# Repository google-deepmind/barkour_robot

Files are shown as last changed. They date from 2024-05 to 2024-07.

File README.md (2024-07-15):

# Barkour Robot

The Barkour Robots are a series of agile quadruped robots developed by Google
DeepMind to support various research projects.

This repository contains the design assets (CAD, PCBA designs, assembly
instructions...) and core software (firmware and low level code) of the Barkour
robots.

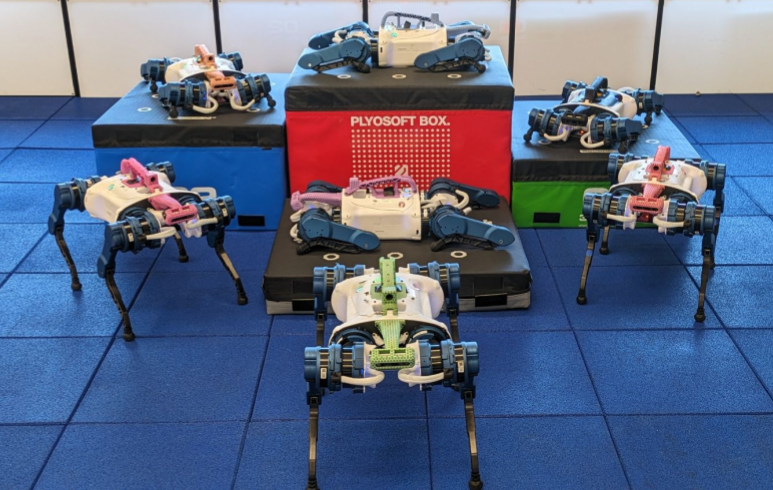
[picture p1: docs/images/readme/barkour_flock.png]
Barkour Robots Hanging Out


## Contents

Detailed documentation is available in the `docs/` folder:

*   [Robot getting started/basic usage guide](docs/getting_started.md)
*   Software:
    *   [Embedded software (firmware)](docs/firmware.md)
    *   [Configuring EtherCAT](docs/ethercat_config.md)
    *   [Motor control example](docs/motor_control.md)
*   Hardware:
    *   [Hardware overview and specs](docs/hardware_overview.md)
    *   [Electronics (PCBA) design files](hardware/electronics)
    *   [Range of motion](docs/barkour_rom.md)
    *   [Cable assembly drawings (WireViz)](hardware/cable_drawings)
*   Robot assembly guides:
    *   [Barkour robot assembly](docs/full_barkour_robot_assembly.md)
    *   [Actuator assembly and setup](docs/actuator_assembly_and_setup.md)
    *   [Hip cover assembly](docs/hipcover_assembly_instructions.md)
    *   [Leg linkage assembly](docs/leglinkage_assembly_instructions.md)
    *   [Wireless E-stop (STO) assembly](docs/wsto_assembly.md)
    *   [IMU configuration](docs/imu_config.md)
    *   [Actuated head assembly](docs/actuated_head_assembly.md)

Mechanical CAD files and simulation environments are available at the following
links:

*   [CAD model](https://gdm.onshape.com/documents/2587dbf423d784b45437b14a/v/b07bb08c3dc8b02bae21b866/e/bdcd5797385cee9e4f78dfef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)
*   Simulation:
    *   [MuJoCo model](https://github.com/google-deepmind/mujoco_menagerie/tree/main/google_barkour_vb)
    *   [MJX tutorial](https://github.com/google-deepmind/mujoco/blob/main/mjx/tutorial.ipynb)

### Mechanical design (CAD models)

We release 2 versions of the Barkour Robot. One version has a fixed head, the
other has an actuated head with a mouth (gripper). You can find the
[CAD models here](https://gdm.onshape.com/documents/2587dbf423d784b45437b14a/v/b07bb08c3dc8b02bae21b866/e/bdcd5797385cee9e4f78dfef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)
for both versions.

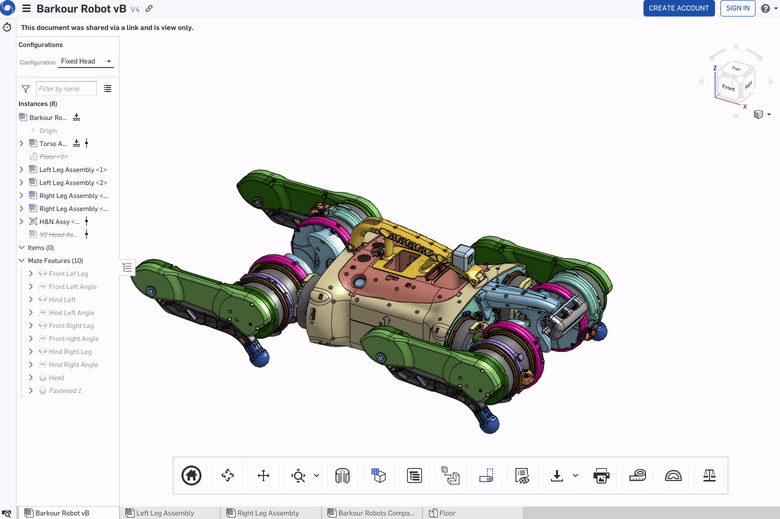
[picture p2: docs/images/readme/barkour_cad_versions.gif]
Barkour Robot CAD Model


### Hardware Usage

Please take a look at the [getting started guide](docs/getting_started.md).

### Simulation

The simulation models were previously released as part of the MuJoCo
[Menagerie](https://mujoco.readthedocs.io/en/stable/models.html). You can find
the MuJoCo model
[here](https://github.com/google-deepmind/mujoco_menagerie/tree/main/google_barkour_vb).

We support MJX for fast training on GPUs and TPUs. Please take a look at the
[MJX tutorial](https://github.com/google-deepmind/mujoco/blob/main/mjx/tutorial.ipynb)
to train a policy in minutes.

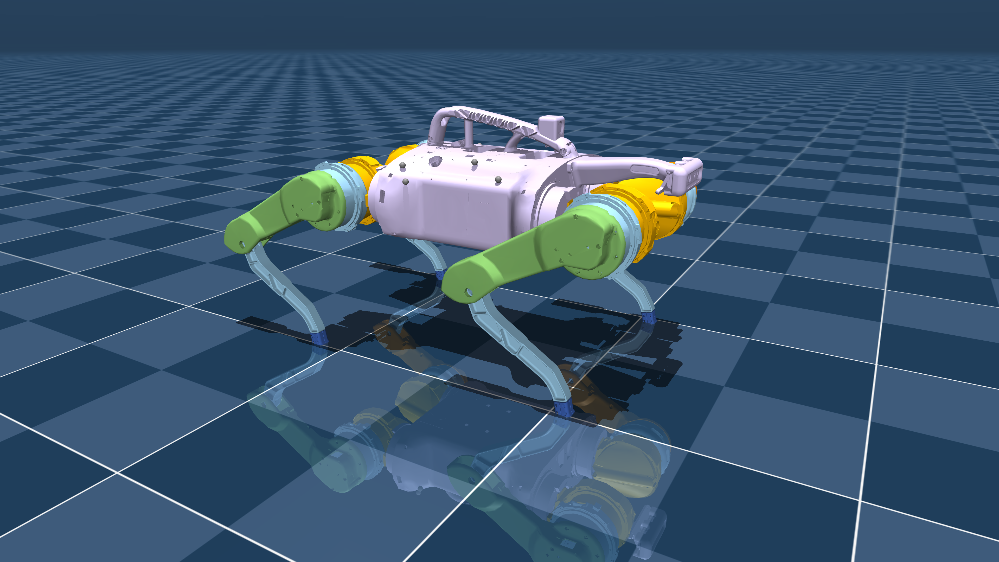
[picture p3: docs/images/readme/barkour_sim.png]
Barkour Robot Sim Model


### Electronics designs (PCBA)

We are including the schematics and PCB layout files for the custom electronics
on the Barkour robots. Take a look in the `hardware/electronics` folder.

You can find drawings of all custom cable assemblies in the
`hardware/cable_drawings` folder.

The Barkour robots use a custom motor driver that communicates with an on-board
computer over EtherCAT:

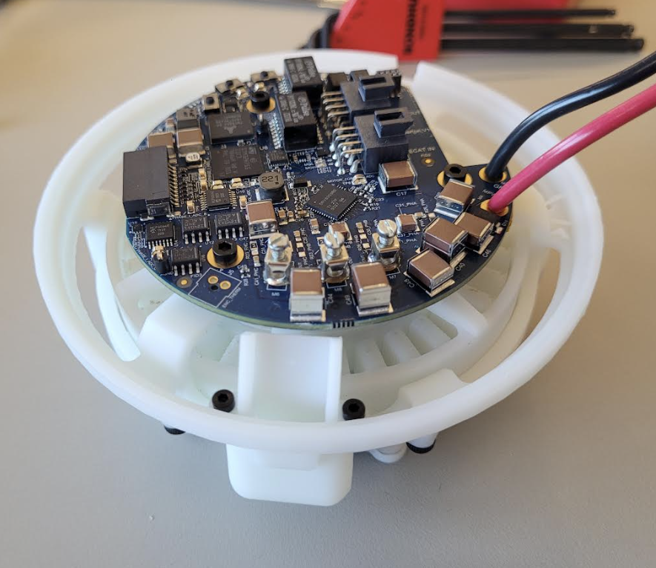
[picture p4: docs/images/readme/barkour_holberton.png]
Barkour Robot Motor Driver


### Assembly guides

We have a complete robot assembly guide to build robots from scratch. Take a
look at the following assembly guides:

-   [Barkour robot assembly](docs/full_barkour_robot_assembly.md)
-   [Actuator assembly and setup](docs/actuator_assembly_and_setup.md)
-   [Hip Cover Assembly instruction](docs/hipcover_assembly_instructions.md)
-   [Leg Linkage Assembly Instructions](docs/leglinkage_assembly_instructions.md)
-   [Wireless E-stop (STO) assembly](docs/wsto_assembly.md)

and here for the
[Bill of Materials (BOM)](hardware/barkour_robot_bill_of_materials.csv).

If you are curious about the actuated head, you can find the assembly
instructions [here](docs/actuated_head_assembly.md)

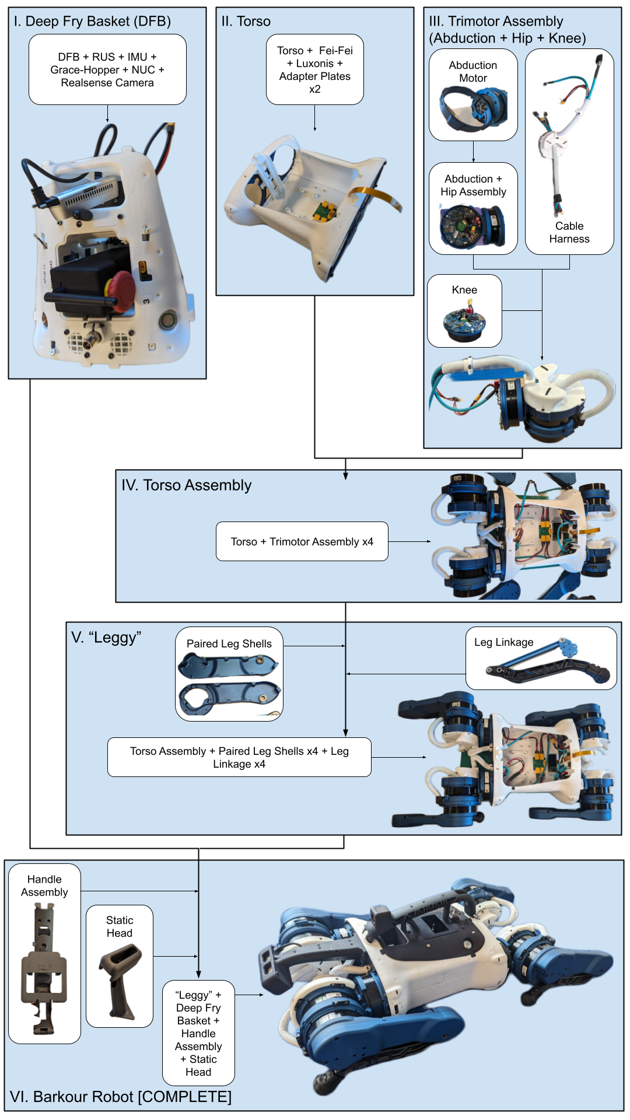
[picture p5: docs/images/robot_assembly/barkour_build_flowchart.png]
Barkour Robot Build Flowchart


### Embedded software and host side software

The Barkour motor drivers use custom firmware based on the
[Pigweed](https://pigweed.dev) open-source project. You can find the firmware in
the `actuator/firmware` folder and our firmware guide [here](docs/firmware.md).
We also provide [a hostside example](docs/motor_control.md) to control the
actuators via EtherCAT and a guide to
[configure EtherCAT](docs/ethercat_config.md).

## Hardware capabilities

The gifs below illustrate the hardware capabilities of the Barkour Robot
platform:

Two leg jump
Four leg jump
Dancing
Jump turn
Manipulating box lid
Pushing a cup of espresso
Push compensation
Tilt compensation
Picking up slippers
Closing dishwasher
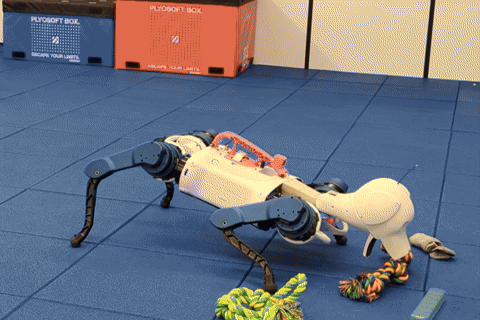
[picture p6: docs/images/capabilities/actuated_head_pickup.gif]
Picking up a toy

Picking up a pillbox
Picking up a shirt and dropping it off
Box climbing
Language to reward

## Older versions

This release contains the "vB" version of the Barkour Robot. As part of our
earlier work, we used an older version of the hardware, called "v0". You can
find the assets for the v0 version at the following links:

-   [CAD](https://gdm.onshape.com/documents/8bcc0544056aa5de830b6353/w/9f4df6916bccef9b9b882a52/e/9296b0bcf28e5f27569d4cdb),
-   [simplified CAD for URDF export](https://deepmind.onshape.com/documents/bd3aaf26c384d7d058cee090/w/9bd0468bf4dae717e9b02f17/e/6151d1e161dfa46066201d62),
-   [sim](https://github.com/google-deepmind/mujoco_menagerie/tree/main/google_barkour_v0),
-   [Barkour obstacle course sim](https://github.com/google-deepmind/mujoco_menagerie/tree/main/google_barkour_v0),
-   [Barkour course scoring script](https://github.com/google/brax/blob/main/brax/experimental/barkour/score_barkour.py).

## Citing this work

If you like this work or make use of our designs, please cite:

```latex
@article{caluwaerts2023barkour,
  title={Barkour: Benchmarking animal-level agility with quadruped robots},
  author={Caluwaerts, Ken and Iscen, Atil and Kew, J Chase and Yu, Wenhao and Zhang, Tingnan and Freeman, Daniel and Lee, Kuang-Huei and Lee, Lisa and Saliceti, Stefano and Zhuang, Vincent and others},
  journal={arXiv preprint arXiv:2305.14654},
  year={2023}
}
```

## License and disclaimer

Copyright 2024 DeepMind Technologies Limited

All software is licensed under the Apache License, Version 2.0 (Apache 2.0); you
may not use this file except in compliance with the Apache 2.0 license. You may
obtain a copy of the Apache 2.0 license at:
https://www.apache.org/licenses/LICENSE-2.0

All other materials are licensed under the Attribution-NonCommercial 4.0
International (CC BY-NC). You may obtain a copy of the CC BY-NC license at:
https://creativecommons.org/licenses/by-nc/4.0/legalcode

Unless required by applicable law or agreed to in writing, all software and
materials distributed here under the Apache 2.0 or CC BY-NC licenses are
distributed on an "AS IS" BASIS, WITHOUT WARRANTIES OR CONDITIONS OF ANY KIND,
either express or implied. See the licenses for the specific language governing
permissions and limitations under those licenses.

This is not an official Google product.

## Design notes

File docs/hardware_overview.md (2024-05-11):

# Hardware Overview

[TOC]

This page provides an overview of how the Barkour robots fit together.

## High-Level Hardware Specs

<table>
  <tr>
   <td>Weight
   </td>
   <td>≈ 14kg
   </td>
  </tr>
  <tr>
   <td>Onboard computer
   </td>
   <td>NUC11TNBv7
   </td>
  </tr>
  <tr>
   <td>Joint torque (nominal/peak)
   </td>
   <td>9Nm, ≥ 18Nm
   </td>
  </tr>
  <tr>
   <td>Joint velocity (peak)
   </td>
   <td>≥ 25rad/s
   </td>
  </tr>
  <tr>
   <td>Motor/battery voltage
   </td>
   <td>30-60V
   </td>
  </tr>
  <tr>
   <td>Sensor/compute voltage
   </td>
   <td>24V (max 200W, about 100W available)
   </td>
  </tr>
  <tr>
   <td>Bus
   </td>
   <td>EtherCAT (typically 1kHz bus cycle)
   </td>
  </tr>
  <tr>
   <td>Camera sensors
   </td>
   <td>RealSense d435i and Luxonis board with OAK-FFC camera module
   </td>
  </tr>
  <tr>
   <td>IMU
   </td>
   <td>1x 3DMCV7-AHRS (torso) + 12x LSM9DS1/LSM6DSO (motor drivers)
   </td>
  </tr>
  <tr>
   <td>Connectivity
   </td>
   <td>2x USB-C (Thunderbolt/USB4), 2.5Gb/s Ethernet (M12 connector), WiFi 6, Bluetooth 5.1, TP-Link UE306 Gigabit Ethernet Network Adapter (USB-to-RJ45) for EtherCAT.  <br/>
See NUC specs for additional connectivity available inside the torso.
   </td>
  </tr>
  <tr>
   <td>Motor
   </td>
   <td>T-motor AK80-9
   </td>
  </tr>
  <tr>
   <td>Wireless STO (E-stop) range
   </td>
   <td>≥ 50m
   </td>
  </tr>
</table>

Looking for the joint ranges or coordinate frame definitions? See
[Motion Conventions and Range of Motion](barkour_rom.md).

## System Diagram

The system diagram below shows the connectivity between the various parts of the
robot, mainly from an electrical point of view. It's a good place to start if
you want to understand how the robot works.

Archived version of system diagram

### NUC Port Allocation

Port allocation and cable selection should be kept consistent for all Barkour
robots.

Archived version of NUC port allocation diagram

### Torso Design Concept

The 3D printed torso consists of two main components: the torso (shell) itself
and the electronics basket.

## Motors

We are using a slightly modified version of the
[T-Motor AK80-9](https://store.tmotor.com/goods.php?id=982). Our variant has an
embedded thermistor and beefed up fasteners to prevent screws from coming loose.

We are not using the T-motor provided motor driver, but rather pair the motor
with the Gebru and Cortes boards (driver) and the Ada board (encoder), or the
Holberton board (driver + encoder).

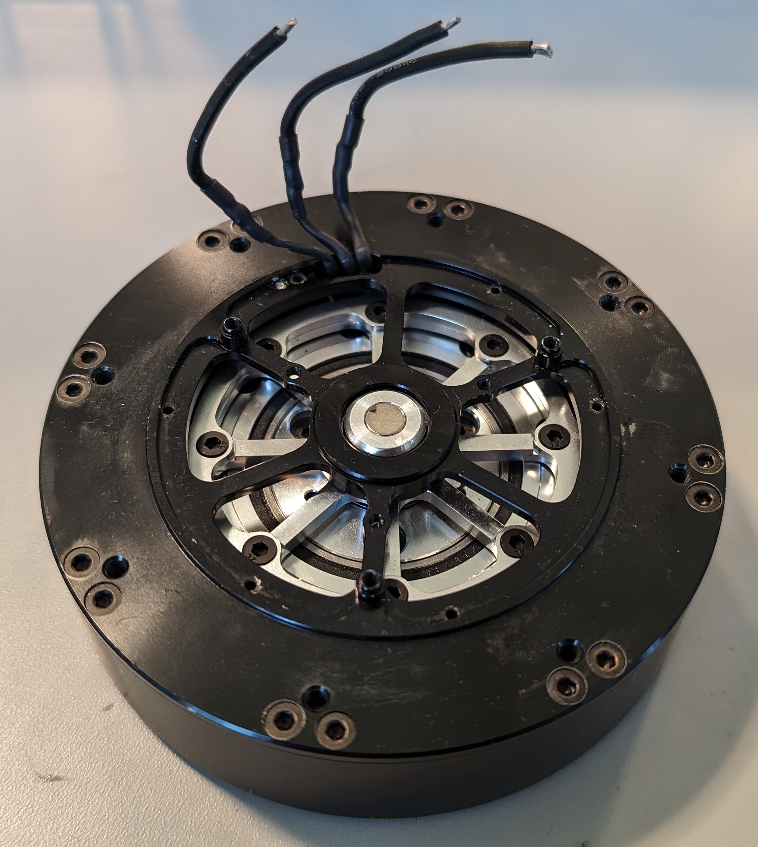
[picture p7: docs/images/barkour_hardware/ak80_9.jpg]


## Dynamixels

When the actuated head is installed, the robot also has 3 XH430-W350T dynamixel
motors. See [actuated head assembly doc](actuated_head_assembly.md) for installation
information and additional details.

## Electronics

The source of truth for electronics designs is in `hardware/electronics`. We
provide Altium source files for all PCBAs listed below.

### PCBAs

#### Cortes & Gebru (Motor Driver)

Cortes and Gebru are stacked boards on the back of each motor. The Gebru board
contains the gate driver; The Cortes board contains the microcontroller,
sensors, and connectivity (EtherCAT).

In addition to the main motor control functionality, the Cortes board comes with
a number of additional sensors. For example, it has a 9 DoF IMU.

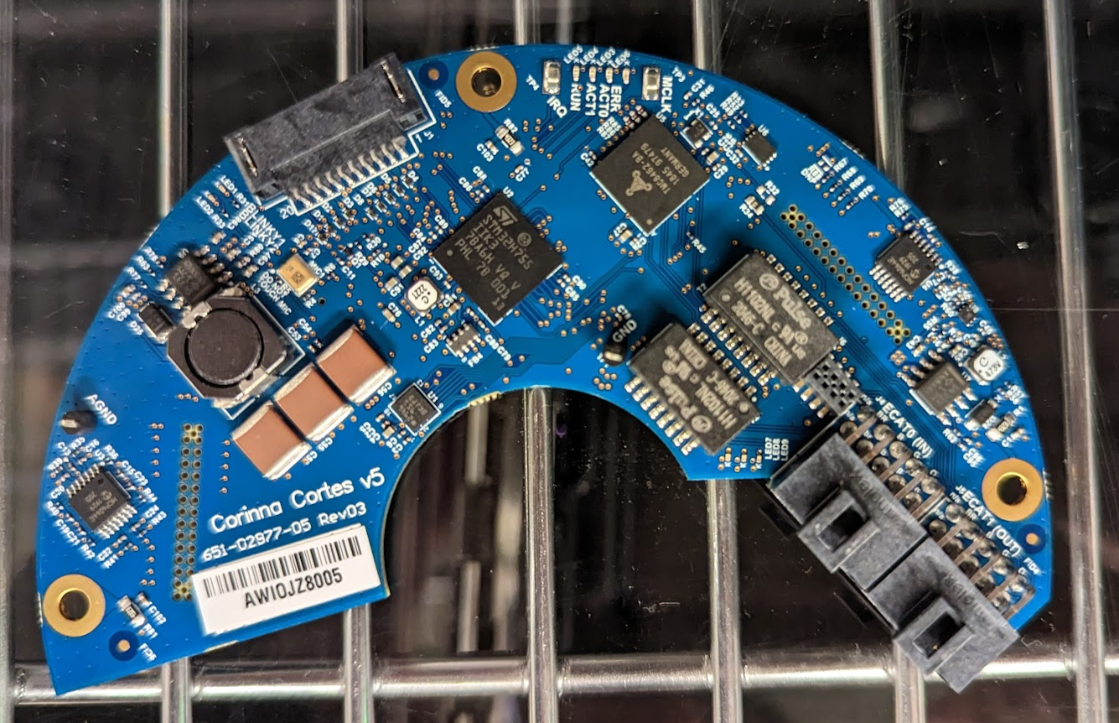
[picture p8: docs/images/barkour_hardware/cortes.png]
Cortes PCBA

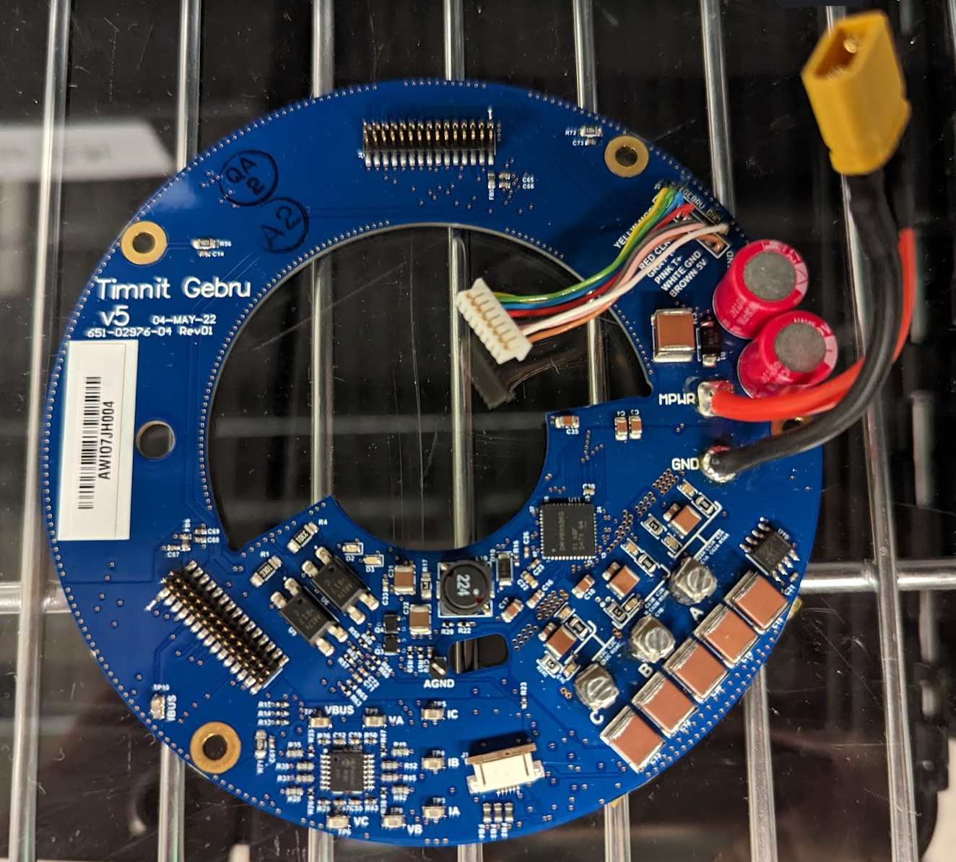
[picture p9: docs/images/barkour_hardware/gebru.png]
Gebru PCBA


#### Ada (Encoder)

This is the encoder board based on the
[MA732](https://www.monolithicpower.com/en/ma732.html) sensor. In addition to
the encoder chip, it also provides connectivity for the thermistor on the motor.

Note: The pinout of the Ada board is compatible with the
[RLS Aksim-2 encoder](https://www.rls.si/eng/aksim-2-off-axis-rotary-absolute-encoder).

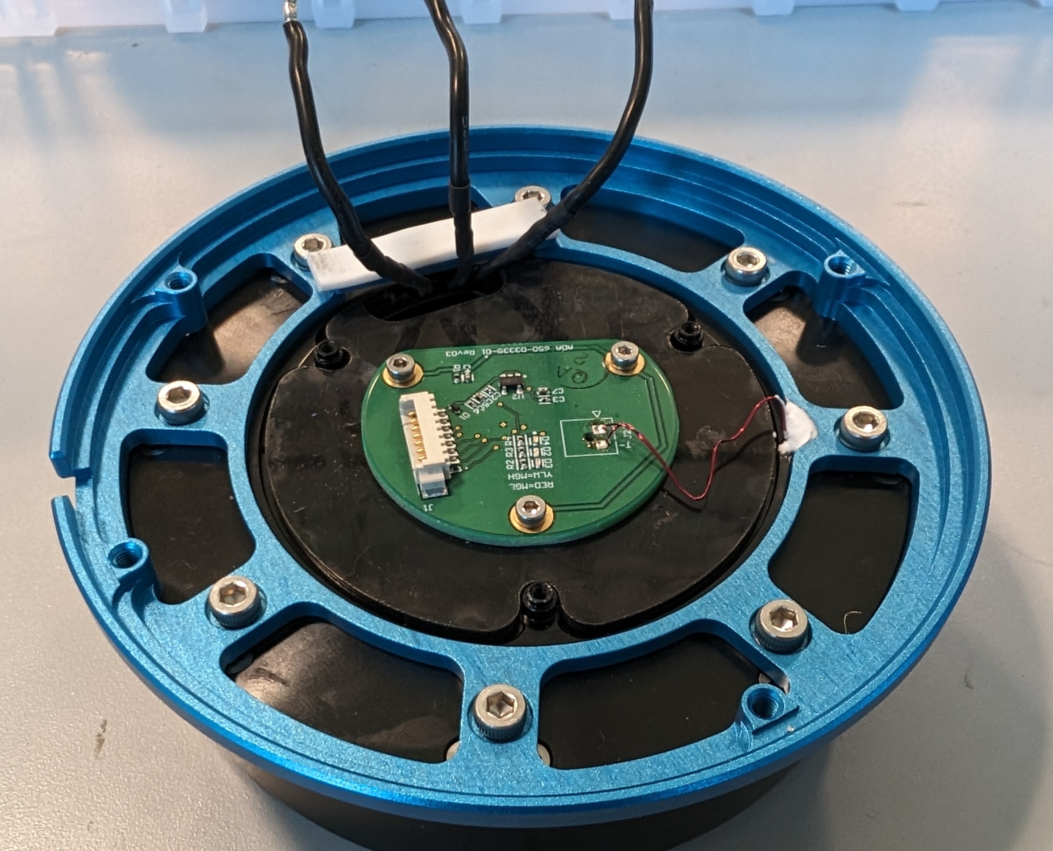
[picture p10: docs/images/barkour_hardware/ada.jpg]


#### Holberton (Single Board Motor Driver)

The Holberton board is a newer generation of the motor driver. It is a single
board replacement for the Gebru/Cortes/Ada stack and the firmware will
transparently run on either variant. Except for the use of different connectors,
the Holberton is a drop-in alternative for the Gebru/Cortes/Ada combo.

Holberton Motor Driver

The Holberton uses 2x4 Nanofit connectors for the EtherCAT and STO
connectivity, rather than the 2x4 connectors used on the Cortes. The pinout is
identical as 2 pins are unused on the Cortes connectors.

The Holberton uses a smaller debug/programming connector than the Cortes board.
The Mataric board has support for both the Cortes and Holberton variants.

The board is rated for up to 75V/50A peak. We limit the current to 20A for
everyday use.

#### Grace & Hopper (Wireless STO)

These boards implement the wireless STO (E-stop) functionality. The Grace board
is the off-robot transmitter; The Hopper board is the receiver inside the
robot's torso.

Note: The Grace and Hopper boards are paired. Each robot has its own E-stop.

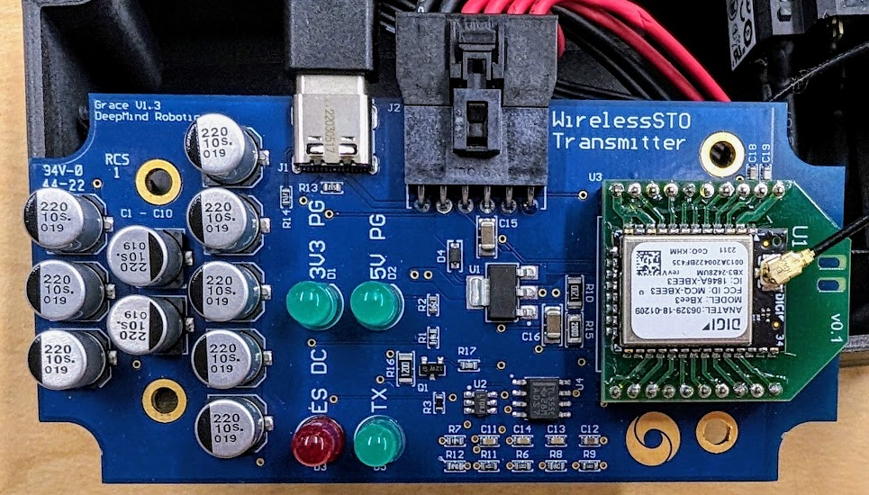
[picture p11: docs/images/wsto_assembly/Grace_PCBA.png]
Grace PCBA

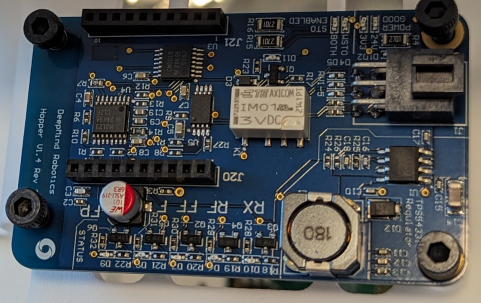
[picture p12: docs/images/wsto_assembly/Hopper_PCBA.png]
Hopper PCBA


#### Hamilton (IMU Breakout)

The Hamilton board is a small breakout board for the torso IMU. It has a
USB-to-serial converter to enable communication with the IMU:

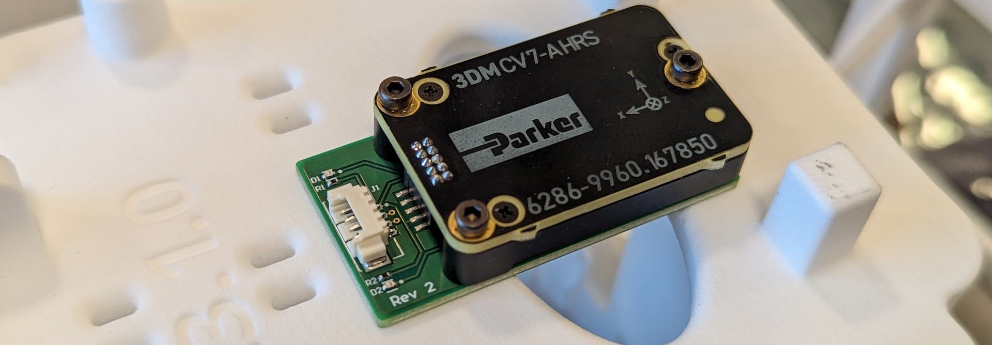
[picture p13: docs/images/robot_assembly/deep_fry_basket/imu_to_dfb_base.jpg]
Hamilton PCBA


#### Jackson (Actuated Head)

The Jackson board controls the actuated head. More precisely, this board:

-   Controls Dynamixel motors (like a [U2D2](https://www.robotis.us/u2d2/)).
-   Powers Dynamixel motors by stepping down the battery voltage. and using a
    single USB C connection.
-   Provides a USB 3 passthrough for the OAK cameras in the actuated head.
-   Provides USB hub functionality.
-   Has an audio amplifier (e.g. to power a small speaker).

Note that the Jackson board is only used with the actuated head robot variant.

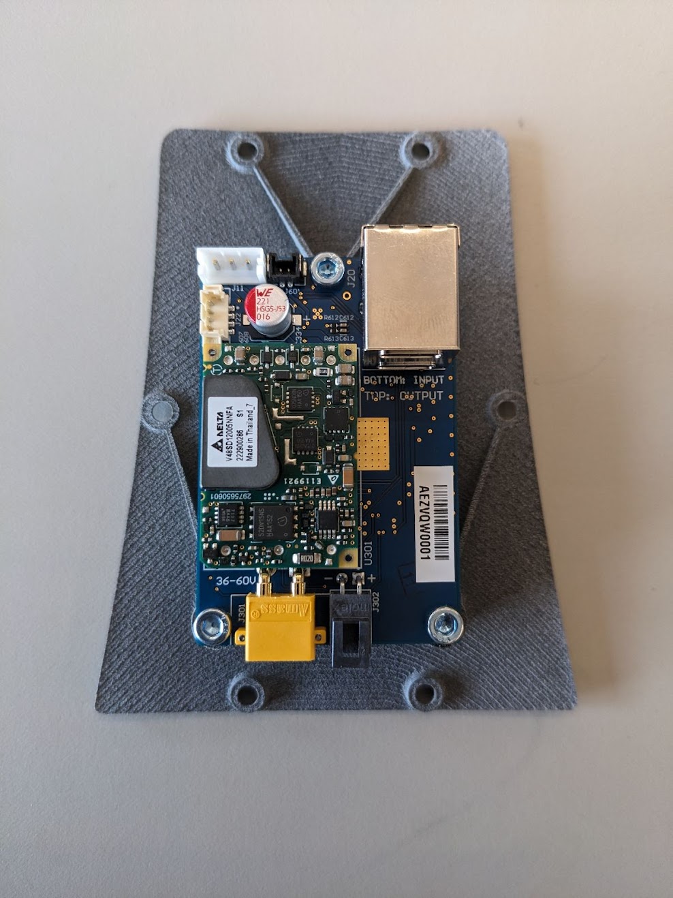
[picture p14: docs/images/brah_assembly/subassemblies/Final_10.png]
Jackson PCBA


#### Fei-Fei (Power Distribution)

This is a very simple board that splits the input power (battery) 4 ways (1 XT60
output per leg), with 2 additional lower-current (XT30) outputs for auxiliary
devices.

The image below shows an earlier version of the Fei-Fei board without the 2 XT30
connectors. The most recent version has 2 XT30 connectors in the center, one of
which is used to power the Jackson board in case the actuated head is installed.

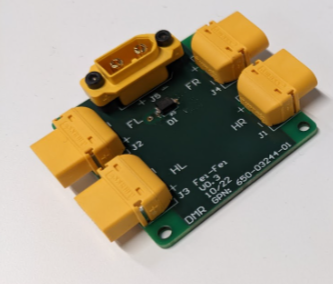
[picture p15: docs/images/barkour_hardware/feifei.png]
Fei-Fei PCBA


#### Mataric (Cortes/Gebru/Holberton Debug/Programming Board)

The Mataric board provides debug buttons and LEDs for the Cortes & Gebru or
Holberton motor driver. Combined with a J-Link, it is also used to flash new
firmware and configure the electrical and joint angle offsets when replacing
motors.

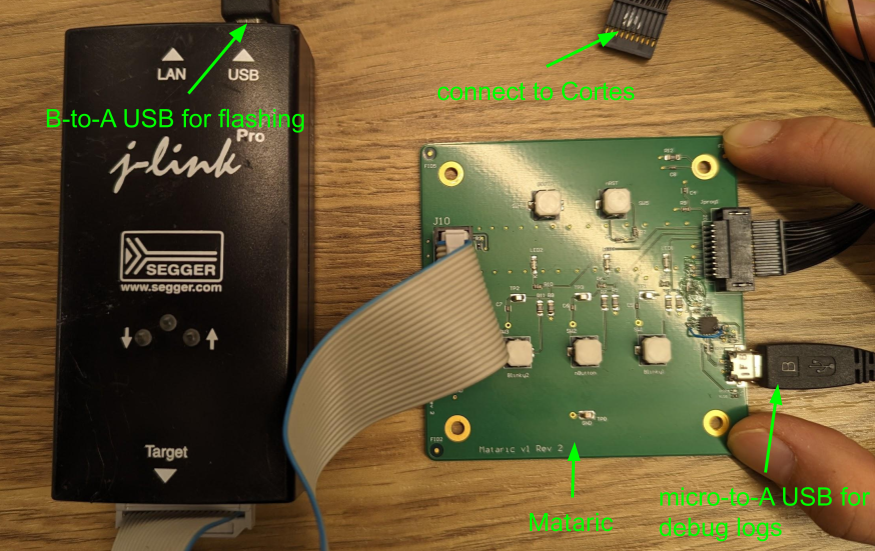
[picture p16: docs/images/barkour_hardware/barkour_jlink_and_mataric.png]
Mataric PCBA


#### Rus (Power Distribution & Conversion)

The Rus board has multiple functions:

-   Convert the battery voltage to 24V (isolated) for the onboard computer &
    sensors.
-   Provide backup power to the 24V circuit (via exposed XT30 connector) to keep
    the onboard computer & sensors up when swapping batteries.
-   Inrush current protection for the motor drivers.
-   Connectors and 24V power for the STO circuit.

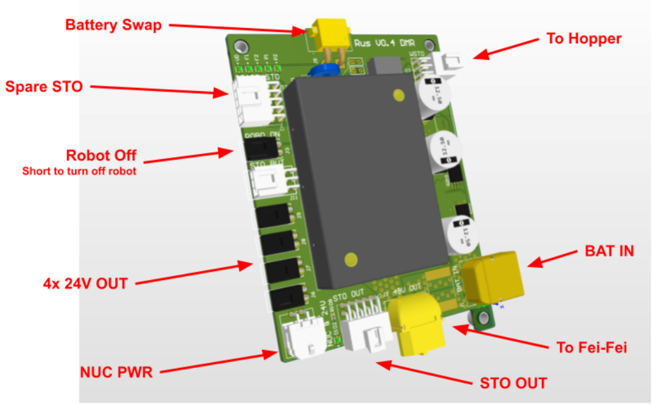
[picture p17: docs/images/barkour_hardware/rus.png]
Rus PCBA


### Battery

We are using off-the-shelf batteries made by DeWalt. The battery voltage is 60V
(15 cell lithium ion). The battery capacity is approximately 122 Wh.

The battery is available in both the UK and the US. However, they are sold under
different manufacturer part numbers:
[DCB606 (US)](https://www.dewalt.com/product/dcb606/flexvoltr-2060v-max-battery-pack-60ah-2-pk)
and
[DCB546 (UK)](https://www.dewalt.co.uk/product/dcb546-xj/xr-flexvolt-6ah-battery).

Note: The DeWalt batteries come in yellow and black housings. These two versions
can be used interchangeably. There is also a larger version of the battery pack,
which looks nearly identical, but won't fit inside the torso.

We use a battery swapper cable to swap batteries in the robot without shutting
down the onboard computer. These click to the DeWalt batteries. The XT30
connector on the swapper cable connects to the external power port next to the
robot's battery slot:

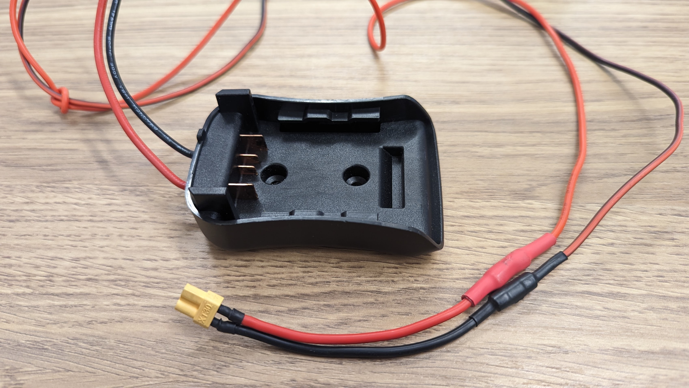
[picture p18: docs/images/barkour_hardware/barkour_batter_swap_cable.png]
Battery swap cable


### Onboard Computer

We are using an
[Intel NUC11tnbv7](https://www.mouser.com/datasheet/2/612/NUC11TN_TechProdSpec-2303479.pdf)
as the onboard computer. The NUC controls the EtherCAT bus and talks to the
onboard sensors (e.g. camera/IMU).

CPU
:   [Intel Core i7-1185G7](https://ark.intel.com/content/www/us/en/ark/products/208664/intel-core-i71185g7-processor-12m-cache-up-to-4-80-ghz-with-ipu.html)

Wifi
:   WiFi 6
    [AX201](https://www.intel.com/content/www/us/en/products/sku/130293/intel-wifi-6-ax201-gig/specifications.html)

RAM
:   Kingston FURY Impact 64GB (2x32GB) 3200MT/s DDR4 CL2 KF432S20IBK2/64
    [Kingston](https://www.kingston.com/datasheets/KF432S20IBK2_64.pdf)

SSD
:   Kingston 2048G KC3000 PCIe 4.0 NVMe M.2 SSD
    [Kingston](https://www.kingston.com/en/ssd/kc3000-nvme-m2-solid-state-drive)

#### Additional USB Devices

The NUC has a number of unused USB ports. Two USB-C ports are routed to the
outside of the robot. The external ports support USB4 and Thunderbolt (e.g. you
can connect an external screen).

### Sensors

#### Torso IMU

The torso contains a IMU 3DMCV7-AHRS. See [IMU config](imu_config.md) for the
setup procedure.

The IMU is located below the battery inside the torso as shown below. It might
be a bit confusing that the X-axis shown on the device points to the back of the
robot. This is intentional. See
[Motion Conventions and Range of Motion](barkour_rom.md) for details about the
coordinate frames.

IMU location

#### RealSense Head Camera

When the robot is equipped with the static head, it uses an Intel RealSense
d435i. See [robot assembly doc](full_barkour_robot_assembly.md) for details.

#### OAK Camera

There is an OAK-FFC-OV9782-M12 camera on the handle of the robot. This camera
attaches to a Luxonis OAK-FFC 4P board. See
[robot assembly doc](full_barkour_robot_assembly.md) on how this is set up for a
static head. For an actuated head, there are 2 OAK cameras. See
[actuated head assembly doc](actuated_head_assembly.md) for details.

## Cabling

Cable drawings can be found in the `/hardware/cable_drawings` directory.

Here's an overview of the main cable types and connectors you might encounter
when using a Barkour robot:

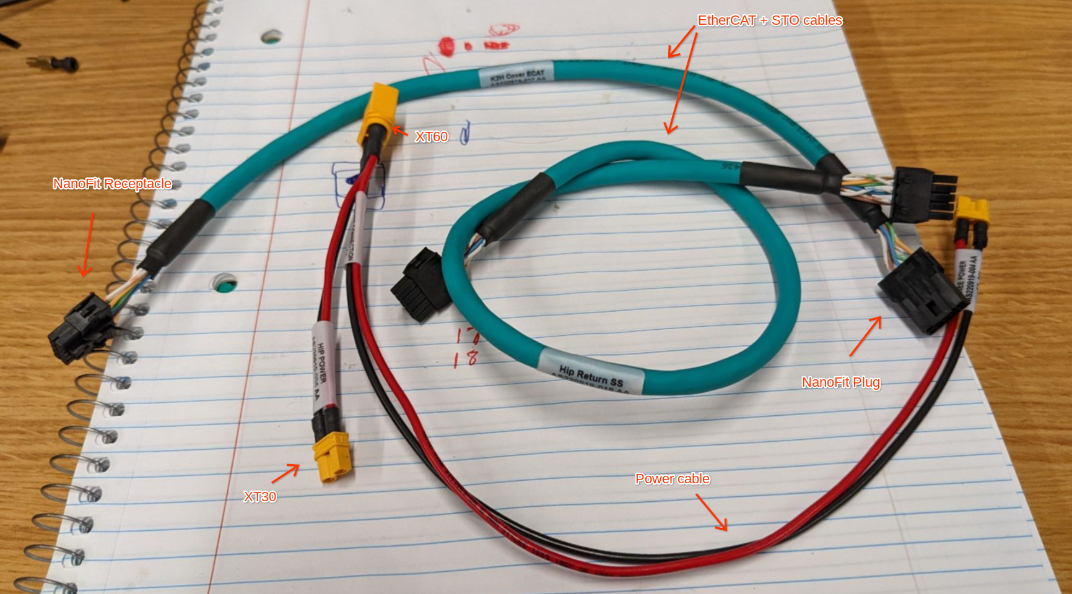
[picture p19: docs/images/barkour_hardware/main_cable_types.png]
Main Cable Types


### Power Cables

These are red and black cables with XT30 or XT60 connectors. They are connected
to the battery in a star topology.

Important: Do not operate the robot with a damaged (e.g. exposed copper) power
connector or cable!

Important: Do not touch the exposed copper (e.g. connector pins) on the
XT30/XT60 connectors (60V ⚡).

### EtherCat and STO Cables (ECAT/STO)

The teal cables
([AlphaWire 76030](https://www.alphawire.com/Products/cable/xtra-guard-performance-cable/Xtra-Guard-Industrial-Ethernet-Flex/76030))
with
[Molex NanoFit](https://www.molex.com/molex/products/family/nanofit_power_connectors)
connectors transfer the EtherCAT and STO signals.

The ECAT/STO connectors and cables are easy to inspect due to the use of 4
colored twisted pairs (CAT5E cable). The top row on each connector only has
solid colored wires (orange, green, blue, brown), whereas the bottom row has
their striped counterparts (orange/white, green/white, blue/white, brown/white).
Pins 5 and 10 (2 rightmost pins) are unconnected by design.

The orange and green pairs carry the EtherCAT signals and the blue and brown
pairs are used for the STO signals. The image below show the wiring diagram for
a typical EtherCAT and STO cable:

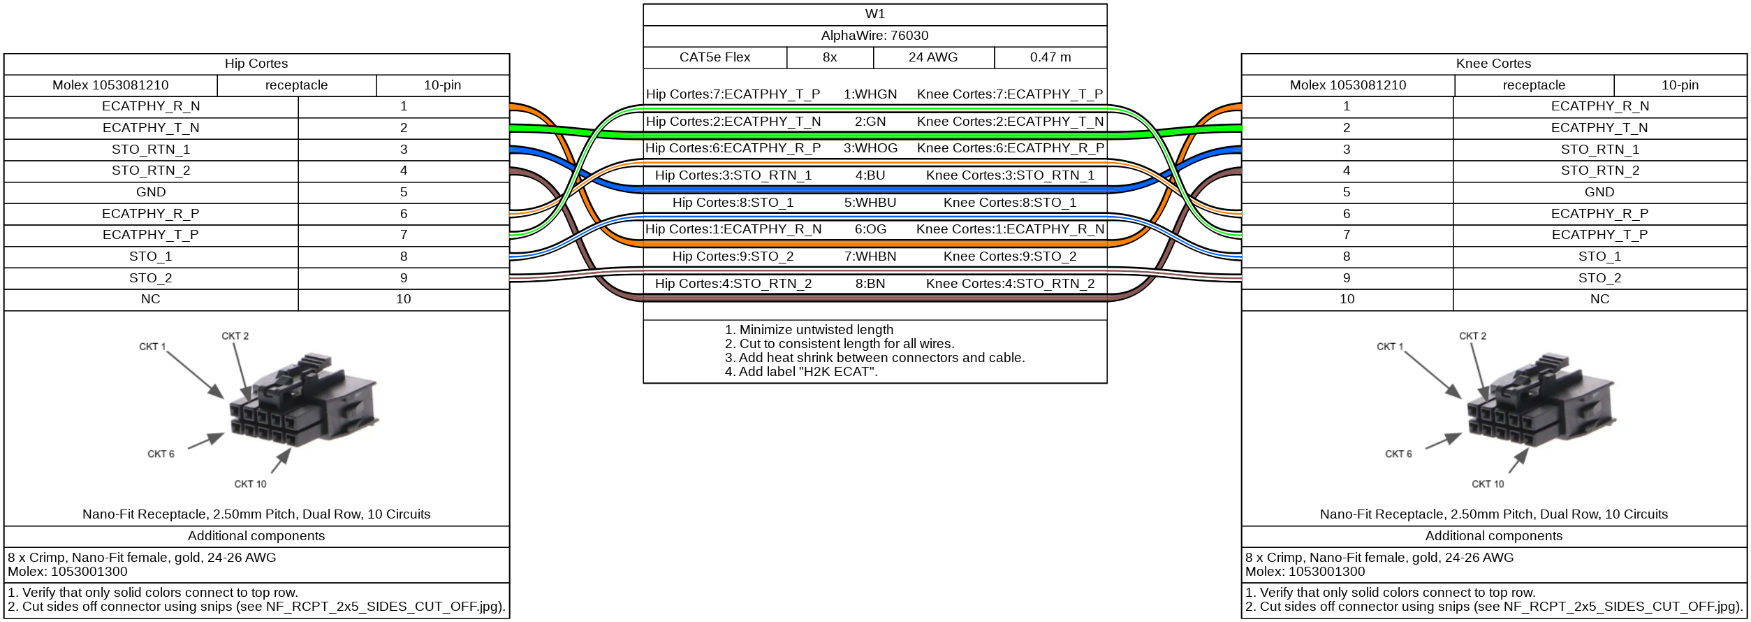
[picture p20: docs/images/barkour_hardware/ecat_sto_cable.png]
EtherCAT and STO cable


The ECAT/STO cables are daisy-chained from motor driver to motor driver. Each
motor driver has an input and output connector and each cable end is labeled
with I (input) or O (output). The chain starts at the NUC, which provides the
EtherCAT signals to the first motor (front left abduction). The last motor in
the chain is connected to the Rus board, which provides the STO signal.

If you follow the ECAT/STO cables on the robot (e.g. take another look at the
system diagram), you might notice that the daisy chain goes from NUC, to front
left, to front right, to hind right, to Rus. However, the canonical leg order is
front left, hind left, front right, hind right. Indeed, the physical connections
prevent long diagonal connections in the torso. We use EtherCAT aliases to
ensure a logical motor order. See
[Motion Conventions and Range of Motion](barkour_rom.md) for details about the
mapping.

Note: Accidentally swapping an ECAT/STO input and output connection won't damage
the electronics. However, the motors (EtherCAT devices) will logically show up
in a different order.

Important: If you notice a loose pin in a NanoFit connector, do not push it back
in and hope for the best. Replace the cable with a new one or replace the whole
connector (i.e. recrimp all 8 pins and use a new connector).

### External Ethernet Connector

The robot exposes an external ethernet port (image below). Rather than a more
common RJ45 connector, an industrial X-coded M12 connector has been installed to
increase robustness.

There are various M12 to RJ45 cables and adapters available online. We typically
use the PC 1080737 which is a 10m M12 to RJ45 cable.

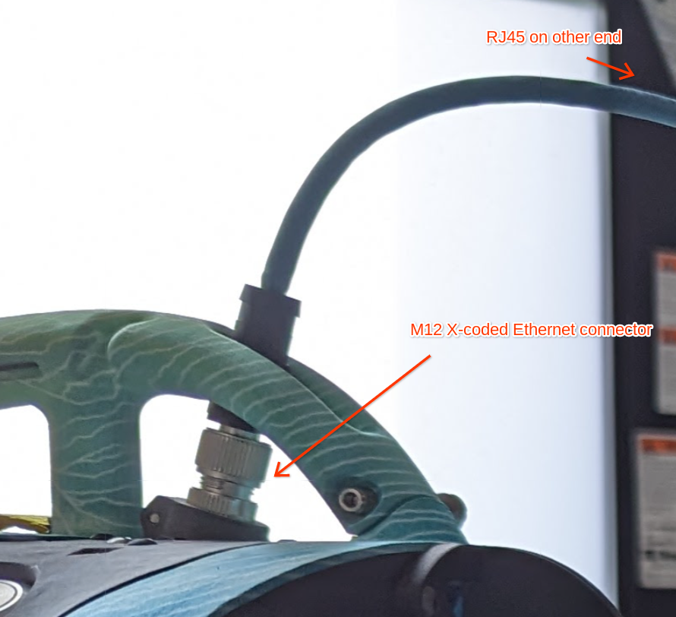
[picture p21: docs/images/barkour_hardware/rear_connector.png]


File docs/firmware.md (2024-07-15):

# Firmware

This page provides instructions to compile, flash, and calibrate the motor
drivers.

The source code can be found in the `actuator/firmware` folder and is based on
the [Pigweed](https://pigweed.dev) framework.

The motor driver is based on the
[STM32H755II](https://www.st.com/en/microcontrollers-microprocessors/stm32h755ii.html),
which is a dual-core (Arm M4 @ 240MHz and M7 @ 480MHz) microcontroller. We are
using the M4 core for the main motor control loop. The M7 core is available for
experimental use. Both cores can communicate with each other using shared
memory. The motor driver uses EtherCAT communication to exchange telemetry and
to receive motor current commands.

Note: The firmware works transparently with either the Holberton or Gebru +
Cortes motor driver variants (see [hardware overview](hardware_overview.md)). No
compilation flags required.

## Compiling the Firmware

Note: We are using [Bazel](https://bazel.build) as the build system. The
instructions below were tested with `bazel 7.1.2` on Debian and Ubuntu.

To build the firmware binaries and helper scripts, run:

```
# From the top-level directory:
bazel build //actuator/firmware/...
```

### Unit Tests

To run the firmware tests on the host, run:

```
# From the top-level directory:
bazel test //actuator/firmware/...
```

## Flashing

There are two ways to flash the motor drivers: using a J-Link connected to the
Mataric debugger board or via EtherCAT (bootloader). If you are flashing the
board for the first time, the J-Link option should be used.

### Flashing the EEPROM (SII)

When bringing up a brand new motor driver, the EtherCAT (TMC8462-BA) chip's
EEPROM has to be flashed to enable EtherCAT communication. Assuming that the
EtherLab library has been [installed](ethercat_config.md), flashing the EEPROM
can be done using the `ethercat` command:

```
cd actuator/ethecat_eeprom
ethercat sii_write -p 0  barkour_robot_sii.hex
```

After rescanning the bus:

```
ethercat rescan
ethercat slaves
```

The device should show up:

```
0   1:0  INIT  E  Cortes
```

Note: The board will be in the error (E) state if no firmware is present on the
microcontroller.

Note: The same SII binary can be used for either the Holberton or Cortes
variants. They will both show up as `Cortes` on the EtherCAT bus.

Important: The provided file uses Google's EtherCAT vendor ID. Update this to
your own [vendor ID](https://www.ethercat.org/en/vendor_id.html) provided by the
EtherCAT Technology Group.

### Flashing with J-Link + Mataric

Connect the Mataric board to the Cortes or Holberton board as shown below:

Mataric PCBA

Run the `helper` script to flash the board:

```
bazel run //actuator/firmware/scripts:helper -- --flash -jlink
```

### Flashing with the EtherCAT Bootloader (Single Device)

To flash a single device, invoke `helper` script providing paths to each
binary and specifying EtherCAT device alias of the device to be updated.

Note: `helper` script must be called from the same machine which built the
script. That is due to multiple dependencies being required at runtime including
external libraries.

```
bazel run //actuator/firmware/scripts:helper -- --flash --tool ecat --m4 <path to m4.bin> --m7 <path to m7.bin> --device_alias <device_alias>
```

An example of updating a single device with expected output:

```
user@ethercat-host:~/binaries_foe$ bazel run //actuator/firmware/scripts:helper -- --flash --tool ecat --m4 new_fw/m4.bin --m7 new_fw/m7.bin --device_alias 3
INFO:absl:Flashing firmware over ethercat
INFO:absl:M4 binary path: new_fw/m4.bin
INFO:absl:M7 binary path: new_fw/m7.bin
INFO:absl:device_alias: 3
INFO:absl:Flashing M7.
INFO:absl:Finished flashing M7.
INFO:absl:Flashing M4.
INFO:absl:Finished flashing M4.
INFO:absl:Power-cycle the device to boot new firmware.
```

Once binaries are successfully transferred to the device over EtherCAT, the
STM32H755 will boot new firmware after being restarted. The most reliable way to
achieve that is by power cycling the device.

Another option is to send a restarting command over EtherCAT directly using the
Etherlab command line:

```
ethercat download -a <device_alias> -t uint32 0x3030 00 0x01234567
```

### Flashing with the EtherCAT Bootloader (All Devices)

To flash all EtherCAT devices, `helper` can be invoked with `--all` flag as
below,

```
bazel run //actuator/firmware/scripts:helper -- --flash --tool ecat --m4 <path to m4.bin> --m7 <path to m7.bin> --all
```

An example of updating all devices with expected output:

```
user@ethercat-host:~/binaries_foe$ bazel run //actuator/firmware/scripts:helper -- --flash --tool ecat --m4 new_fw/m4.bin --m7 new_fw/m7.bin --all
INFO:absl:Flashing firmware over ethercat
INFO:absl:M4 binary path: new_fw/m4.bin
INFO:absl:M7 binary path: new_fw/m7.bin
INFO:absl:Devices (by alias) to reflash: ['1', '2', '3', '7', '8', '9', '10', '11', '12', '4', '5', '6']
INFO:absl:Flashing device 6.
INFO:absl:Flashing M7.
INFO:absl:Finished flashing M7.
INFO:absl:Flashing M4.
INFO:absl:Finished flashing M4.
INFO:absl:Flashing device 5.
INFO:absl:Flashing M7.
INFO:absl:Finished flashing M7.
INFO:absl:Flashing M4.
INFO:absl:Finished flashing M4.
...
INFO:absl:Flashing device 1.
INFO:absl:Flashing M7.
INFO:absl:Finished flashing M7.
INFO:absl:Flashing M4.
INFO:absl:Finished flashing M4.
INFO:absl:Power-cycle the network to boot new firmware.
```

After updating firmware on all devices it is highly recommended to power cycle
the network so that microcontrollers boot with the new firmware. That is because
restarting each device separately, as described in previous section, can disrupt
EtherCAT network and some devices might lose connection. If you are using the
Holberton motor driver, it is possible to power cycle the devices via EtherCAT
(see [here](ethercat_config.md)).

### How FoE Firmware Updates Work

File over EtherCAT is a method of exchanging large volumes of data between via
an EtherCAT bus. It is a mailbox protocol and as such available in all states
except INIT. However, in this implementation FoE is artificially limited to BOOT
state only, since it can cause heavy bus load and impede EtherCAT performance.

FoE is used here to flash new firmware onto the devices. Currently the firmware
is split into two binaries - `m4.bin` and `m7.bin`.

On the device side, FoE is handled by SOES, with the help from some callbacks.
On the host side, FoE is initiated by Etherlab commands. The following
approximate sequence of events is triggered:

1.  User sets device into BOOT (`ethercat state BOOT`).
2.  User initiates FoE data transfer (`ethercat foe_write -a <device_alias>
    m4.bin`).
3.  Interrupt is generated on M4 to inform that an EtherCAT exchange took place.
4.  EtherCAT task wakes up and reads AL event register 0x220. Flag SM0/1 event
    is active.
5.  `ESC_foeprocess()` is called, which in turn calls
    `foe_writefile_cfg_t.write_function()`, which is set to `flash_firmware()`.
6.  `flash_firmware()` processes the incoming data chunk by chunk. This method
    erases flash sectors and writes the new data to the flash memory.

Activation of the firmware is handled separately. A custom `uint32_t` object
dictionary at index `0x3030:00` is used to trigger a bank swap and a device
reboot when `0xDEADC0DE` is written to it. This activates the new firmware. Use
`ethercat download -a <device_alias> -t uint32 0x3030 00 0xDEADC0DE` to do this
manually. Do note that `ethercat rescan` might be needed after a firmware update
to ensure Etherlab is aware of the SDO entry.

### Firmware Organization

The STM32H755 has two identical memory banks of 1 megabyte each (flash bank 1
starting at address `0x08000000` and flash bank 2 starting at address
`0x08100000`). The banks each consist of 8 128 kB sectors.

The flash banks can be swapped, which is transparent to the microprocessor
cores. This means that after a bank swap, bank 1 is now bank 2 and vice versa
and all addresses that used to point to bank 1 now point to bank 2 and vice
versa. We use this mechanism to enable firmware updates. The current firmware is
always running from flash bank 1 and the update tool (`flash_firmware()`) always
writes to flash bank 2. A bank swap causes the new firmware to become active.

The firmware is organized as follows:

```
0x08000000 - 0x0807FFFF: M7 code (max 512 kilobyte).
0x08080000 - 0x080FFFFF: M4 code (max 512 kilobyte).
```

The firmware for each core is compiled separately, resulting in two ELFs and two
BINs. See the `helper` script for details. This is nothing more than a
byte-by-byte copy of the program data.

As the M7 core always boots first, we place its firmware at the start of the
bank (at the default address for the STM32). When the M7 boots up
(`main_m7.cc`), it checks that the boot addresses for the M7 and M4 are correct.
If not, it updates the relevant registers of the STM32 and reboots the device.
When the M4 boots up, it updates the address of the interrupt vector table to
point to the start of its flash memory (the default is located at the start of
the memory bank, so we have to make sure the M4 does not use the M7's interrupt
vector table).

The 50/50 split between the M7 and M4 is just an arbitrary choice and might not
be ideal. To change the boot addresses, update the following files and make sure
that the M4's code starts at the beginning of a flash sector (128 kB):

1.  `flash_firmware()` in `actuator/firmware/barkour/m4/ecat_device.cc`.
2.  The linker files in `actuator/firmware/targets/m4` and
    `actuator/firmware/targets/m7`.
3.  `actuator/firmware/barkour/m7/main_m7.cc` to set the correct boot addresses.

Note: Flash bank 2 can be used for data storage during normal operation. It will
only be overwritten when new firmware is flashed.

## Calibration

### Running Calibration Routines

To run the calibration routines, the Mataric programmer board must be attached
to the motor driver. There are two calibration routines, which are independent
of one another, and must be run separately.

Successful completion of either calibration routine involves a restart of the
EtherCAT stack, to force a write of the calibrated values to EEPROM / SII.
Depending on the state of the EtherCAT host and device stacks at the time of
calibration, this restart can sometimes cause the EtherCAT stack to enter an
error state. Power cycling the motor after calibration will usually resolve any
such issues.

### Electrical Angle Offset

The electrical angle offset is the difference between the encoder zero position,
and the nearest position where the electrical angle of the motor is zero. This
is critical for operation, as the motor cannot be commutated without this
information. It is calculated by applying a fixed set of voltage commands to the
motor to hold its electrical angle to 180 deg, then to 90 deg, and reading the
encoder angle. The final 0 position offset is then calculated and stored.

A validation check is performed to ensure that the motor turned ~90 electrical
degrees during the process, if the measured turn is with 10 Deg the calibration
is considered good, if the rotation was out by more than 10 Deg an error is
reported and the calibration is aborted.

The motor should have no significant load attached to it, and should be placed
in a position where it is able to rotate freely for at least ~15 (mechanical)
degrees in each direction. Ideally it should also be placed such that the axis
of rotation is parallel to gravity.

The routine is triggered by by holding the `nButton` on the Mataric board while
the power is turned on or the `nRST` button is pushed to reset the STM. This
will run the electrical angle calibration, store the calibration results to
EEPROM (as part of the EtherCAT SII), and restart the EtherCAT stack.

During the calibration process the LEDs on the Mataric board will indicate the
status. At the start of calibration the orange Blinky2 LED will be lit. If the
calibration is successful the Blinky2 LED will go out and the board can be
operated normally. If there is an error during calibration the Red Blinky1 LED
will light and the board will enter a hung error state.

Additional debug info is also reported on the pw console output during the
calibration.

The electrical angle offset can be read via SDO, with index `0x3000`, subindex
`0x1`, as an `int32`, with units of encoder counts. The SDO at index `0x3000`,
subindex `0x2`, type `uint8` should read `1` if the calibration has been
completed successfully, and any other value otherwise.

### Joint Angle Offset

The joint angle offset is the difference between a negative-side joint endstop
and a joint zero position.

To run this routine, the robot joint should be held against its negative
endstop, with a Mataric board attached. Then the following sequence of button
presses is needed on the Mataric board: - The reset button pressed and held
(i.e. not let go yet!) - The `Blinky1` button pressed and held. - The reset
button released. - (A few seconds later) the `Blinky1` button released.

This results in the `Blinky1` button being held as the firmware starts up, which
will trigger a series of encoder reads. The median of these will be used as the
zero offset, and stored to EEPROM (as part of the EtherCAT SII). The EtherCAT
stack will then be restarted.

If the calibration routine has been successful, the position of the motor (as
reported over DS402) will be relative to this recorded position.

The joint angle offset can be read via SDO, with index `0x3001`, subindex `0x1`,
as an `int32`, with units of encoder counts. The SDO at index `0x3001`, subindex
`0x2`, type `uint8` should read `1` if the calibration has been completed
successfully, and any other value otherwise.

### Error Reporting

Error codes corresponding to certain error conditions are be written to the
CANopen "manufacturer status register", index `0x1002`, subindex `0x0`. This can
be mapped to a PDO to allow for monitoring errors in the cyclic control loop on
the host side.

This contains a `uint32` value, where the bits are set according to the
following table. The bit indices are given in LSB order.

| Bit Index | Error Condition | Result |
| --- | --- | --- |
| 0 | Electrical angle calibration  | Controller loop stops |
:           : routine failed                :                                 :
| 1         | Joint angle calibration       | Controller loop stops           |
:           : routine failed                :                                 :
| 2         | Calibrated electrical angle   | Controller loop stops           |
:           : offset not found              :                                 :
| 3         | Calibrated joint angle offset | Joint angle offset of `0` used. |
:           : not found                     :                                 :
| 4         | Invalid motor parameters set  | Controller loop stops           |
| 5         | Invalid current limit set     | Current limit set to infinity   |
| 6         | Failed to configure one or    | Controller loop stops           |
:           : more controller components    :                                 :
| 7         | Failed to get sensor readings | Controller loop stops, if this  |
:           : / derived quantities          : is the first read, else CiA 402 :
:           :                               : fault                           :
| 8         | STO enabled                   | CiA 402 fault or failure to     |
:           :                               : initialize                      :
| 9         | Unexpected gate driver state  | CiA 402 fault                   |
:           : change while voltage is       :                                 :
:           : applied to motor              :                                 :
| 10        | EtherCAT not in "operational" | CiA 402 fault                   |
:           : state while CiA 402 state     :                                 :
:           : machine initialized           :                                 :
| 11        | Bus voltage too low           | CiA 402 fault                   |
| 12        | Overheat detected             | CiA 402 fault                   |
| 13        | STO line 1 down while voltage | CiA 402 fault                   |
:           : is applied to motor           :                                 :
| 14        | STO line 2 down while voltage | CiA 402 fault                   |
:           : is applied to motor           :                                 :

The error bits which result in a CiA 402 fault will be reset upon a CiA 402
fault recovery state transition.

Manufacturer status register can be read over EtherCAT using following command

```
ethercat upload -a <alias> -t uint32 0x1002 0x0
```

## Shared Memory Block

The primary mechanism for inter-core communications is a block of shared memory
which both cores can access. We use the SRAM4 block in Domain 3 for this
purpose, which has address range `0x38000000` - `0x3800FFFF`.

This block is recommended by the reference manual to be used for this purpose.
It can also be seen from the linker files that the M4 core uses SRAM1, SRAM2 and
SRAM3 for its working memory, whereas the M7 core uses the AXI SRAM. This means
that SRAM4 is not used by either core for working memory, and so is safe to use
for inter-core communications without the risk of e.g. corrupting the stack.

### Shared Variables

The shared variables, addresses and expected use patterns are listed below. In
code, they are described in the
`actuator/firmware/barkour/common/shared_memory.h` header.

<!-- mdformat off(Multiline tables not rendered by gitiles) -->
| Address | Address Alias in Code | Type | Expected Use Pattern |
| --- | --- | --- | --- |
| `0x38000000` | `kUidWord0Address` | `uint32_t` | Written to by the M7 core on startup, before the M4 core starts. Read-only thereafter. Contains a copy of the STM variable unique identifier word 0, `UID[31\:0]`, which can only be read by the M7 core. |
| `0x38000004` | `kUidWord1Address` | `uint32_t` | Written to by the M7 core on startup, before the M4 core starts. Read-only thereafter. Contains a copy of the STM variable unique identifier word 1, `UID[63\:32]`, which can only be read by the M7 core. |
| `0x38000008` | `kUidWord2Address` | `uint32_t` | Written to by the M7 core on startup, before the M4 core starts. Read-only thereafter. Contains a copy of the STM variable unique identifier word 2, `UID[95\:64]`, which can only be read by the M7 core. |
<!-- mdformat on -->

## EtherCAT Implementation Details

This section describes the implementation details of the EtherCAT stack.

Terminology:

-   ESC: EtherCAT Slave Controller (TMC8462)
-   SII: Slave Information Interface
-   ETG: EtherCAT Technology Group
-   ESCReg: EtherCAT Slave Controller register (see TMC8462 data sheet)

## Implementation of EtherCAT on Cortes using SOES.

SOES is an open source EtherCAT device stack implementation. The kernel state
machine and general device functionality is contained in the following files,
together with their corresponding headers:

```
esc.c
esc.h
esc_coe.c
esc_coe.h
esc_foe.c
esc_foe.h
ecat_slv.c
ecat_slv.h
```

Using SOES requires the following steps:

1.  Implement an interface to the hardware
2.  Specify general configuration options for SOES
3.  Merge everything into your application

### Interface to Hardware

The communication between the ESC and SOES is implemented in these functions:

-   `void ESC_init(const esc_cfg_t *config)`: Initialize hardware
-   `void ESC_read(uint16_t addr, void *buf, uint16_t len)`: Read contents of a
    register
-   `void ESC_write(uint16_t addr, void *buf, uint16_t len)`: Write data to a
    register

The ESC is connected via an SPI bus clocked at 30 MHz.

### Configuration of SOES

The device application is configured in the following header files:

-   `actuator/firmware/barkour/m4/ecat/ecat_options.h`: General options
    configuring the device
-   `actuator/firmware/barkour/m4/ecat/utypes.h`: struct definition for all data
    to be exchanged between the SOES kernel and application.

### Object Dictionary Definition

The EtherCAT object dictionary is defined in
`actuator/firmware/barkour/m4/ecat/objectlist.c`.

## SOES Callbacks and Required Functions

SOES uses a callback mechanism as well as mandatory functions where the user can
implement custom behaviour. These functions are defined in
`actuator/firmware/barkour/m4/ecat_device.cc`. Take a look, it is extensively
documented in source code.

Mandatory are: * `cb_set_outputs()`: Called just after a RxPDO (SM2 event) is
received (host to device) in order to set outputs. Ideally most of the work is
done * here because it is synchronous to RxPDO reception. * `cb_get_inputs()`:
Called just before data is transferred into the output buffer (SM3).

In this application the following optional callbacks are implemented: *
`set_defaults()`: Called in transition INIT->PREOP * `pre_state_change()`:
Called just before a state change. Can be used to perform exit instructions or
to reject the change * `post_state_change()`: Called just after state has
changed, but just before it is acknowledged in the ALstatus register (0x0130) *
`safeoutput()`: Called upon exit of OP state, Error State, etc; used by the
application to ensure outputs are switch to safe state.

These optional callbacks are configured in `struct EthercatDevice` that is
passed to SOES during stack initialization.

## EtherCAT Main Loop

The EtherCAT stack runs in a separate thread on the M4. There is a single entry
point `EthercatDevice::run()`, implemented in
`actuator/firmware/barkour/m4/ecat_device.cc`, which runs forever. First the
stack is configured with `ecat_slv_init()` after which it goes into an infinite
loop, waiting on a semaphore, calling `ecat_slv_poll()` to get EtherCAT status
information and `DIG_process()` to process PDOs.

The loop is interrupt driven. Whenever an EtherCAT packet is received, it
generates an interrupt that releases a semaphore from
`EthercatDevice::EofInterrupt()`. This implementation is thus called
SM-Synchronous.

## EtherCAT Communication

In this section various typical EtherCAT scenarios are described to show how the
implementation reacts.

### SDO

Service Data Objects (SDO) is mailbox communication, similar to remote procedure
calls. Mailbox communication is available in all states except INIT.

Every EtherCAT object defined in the object list can be accessed (read or
written) via SDO.

SDO is handled completely by SOES, with help from some callbacks. The following
approximate sequence of events is triggered:

1.  Server initiates a request (`ethercat upload -p0 0x1000 0`)
2.  Interrupt is generated on M4 to inform that an EtherCAT exchange took place
3.  ECat task wakes up and reads AL event register 0x220. Flag SM0/1 event is
    active
4.  `ESC_coeprocess()` is called, which in turn calls
    `pre_object_download_hook()` and `post_object_download_hook()` where a
    non-zero return value calls SDO abort.
5.  SOES prepares an answer and sends it back to the host.

### PDO

Process Data Objects (PDO) are typically process variables that are exchanged
between host and device on a continuous basis, usually with every EtherCAT
cycle.

As a PDO is an EtherCAT object, it is also a SDO but not the other way round.
Whether an EtherCAT object is a PDO or not is defined in the object dictionary.

During the setup phase in PREOP, the host configures, or maps, PDOs into a
SyncManager using SDO transactions. In fact SyncManager configuration simply
sets up objects 0x1C12 (SM2, Outputs, RxPDO) and 0x1C13 (SM3, Inputs, TxPDO) in
a special way.

PDOs are exchanged during SAFEOP and OP only

PDO is handled completely by SOES, with help from some callbacks. The following
rough sequence of events is triggered:

1.  Server initiates a PDO exchange 1. Interrupt is generated on M4 to inform
    that an EtherCAT exchange took place
2.  ECat task wakes up and reads AL event register 0x220. Flag SM2/3 event is
    active
3.  User calls `DIG_process()` 1. If SM2 event flag is set (outputs, RxPDO), the
    values are read into `struct _Object` struct by SOES. Thereafter
    `cb_set_outputs()` (a user function) is called to inform of the arrival of
    new data 1. User callback `application_hook()` is called
4.  User callback `cb_get_inputs()` is called and SOES copies data out of
    `struct _Object` into the EtherCAT output area to get ready for a TxPDO
    frame.

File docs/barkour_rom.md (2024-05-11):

# Barkour Motion Conventions and Range of Motion

This document describes the range of motions of the Barkour Robot (joint limits
and directions) and the joint ordering.

barkour_motion

## Leg Order & Joint Order

### Leg Order

When referring to the legs by name is not possible, use the following leg order:
\
front left leg = 0, hind left leg = 1, front right leg = 2, hind right leg = 3

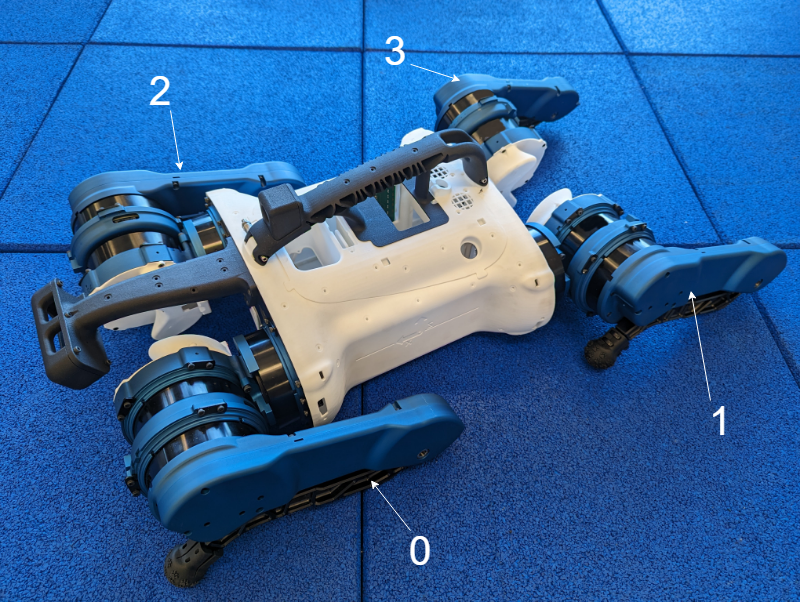
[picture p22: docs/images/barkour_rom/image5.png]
leg order


### Joint Order

When referring to the joints/actuators by name is not possible, use the
following joint order: \
abduction = 0, hip = 1, knee = 2

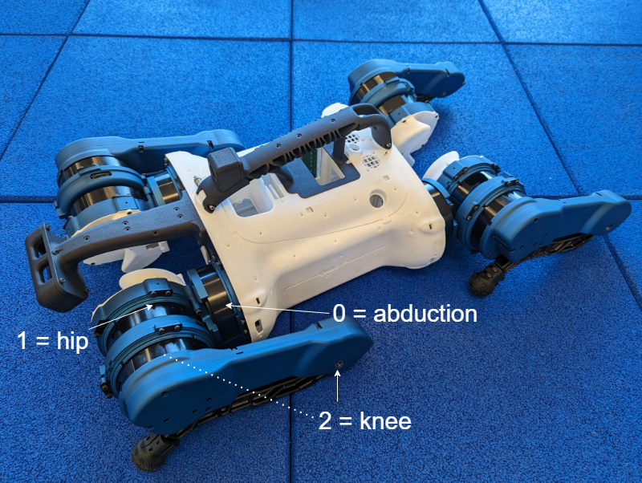
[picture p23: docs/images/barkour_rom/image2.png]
joint order


### Combined Leg and Joint Order

When referring to the joints/actuators and legs by name is not possible, use the
joint order in the following table. If not specified, decimal (base 10) numbers
are used.

The actuators are daisy-chained together in a different order on the EtherCAT
bus, but this is transparent to the user as each motor has an alias that matches
the well-known leg and joint order (with 1-based indexing due to EtherCAT
conventions).

Robot Joint Leg Order | Robot Joint Order | Leg abbr. | Name                    | Actuator Physical Position on ECAT chain | Physical Leg Order (ECAT) | ECAT device alias
:-------------------: | :---------------: | :-------: | ----------------------- | :--------------------------------------: | :-----------------------: | :---------------:
0                     | 0                 | "FL"      | "abduction_front_left"  | 0                                        | 0                         | 1
                      | 1                 |           | "hip_front_left"        | 1                                        |                           | 2
                      | 2                 |           | "knee_front_left"       | 2                                        |                           | 3
1                     | 3                 | "HL"      | "abduction_hind_left"   | 9                                        | 3                         | 4
                      | 4                 |           | "hip_hind_left"         | 10                                       |                           | 5
                      | 5                 |           | "knee_hind_left"        | 11                                       |                           | 6
2                     | 6                 | "FR"      | "abduction_front_right" | 3                                        | 1                         | 7
                      | 7                 |           | "hip_front_right"       | 4                                        |                           | 8
                      | 8                 |           | "knee_front_right"      | 5                                        |                           | 9
3                     | 9                 | "HR"      | "abduction_hind_right"  | 6                                        | 2                         | 10
                      | 10                |           | "hip_hind_right"        | 7                                        |                           | 11
                      | 11                |           | "knee_hind_right"       | 8                                        |                           | 12

Here's a visual representation of the ordering above:



## Barkour Motor Direction Convention

For the individual actuator modules and the associated firmware, the direction
of positive rotation is the rotor moving clockwise with respect to the stator
when looking at the rotor side of the motor. In other words, using the
right-handed rotation convention, the axis of rotation is in the direction from
the rotor towards the stator.

Note: This is not the same as the robot joint directions. There is also no
defined convention for the zero position for a single motor until it is built
into a full robot.

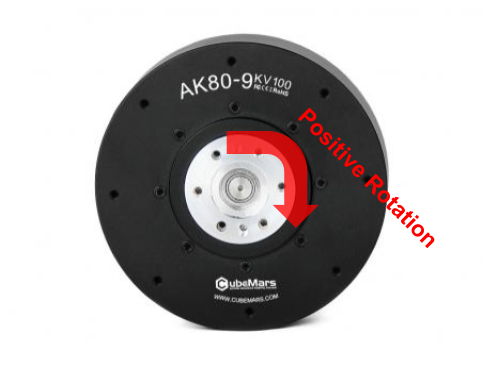
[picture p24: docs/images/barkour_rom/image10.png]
positive rotation


## Barkour Robot Joint--Zero Position

Each joint of the robot has a defined zero position, which is used for control.
The following images show the robot in the configuration where all joints are at
their defined zero positions.

Important: If in doubt, the zero position of the hip joints is such that the
line from the center of the hip pivot to the center of the knee pivot is
horizontal, and the knee joints are fully closed. The “fully closed” knee joint
may look slightly more or less closed than in the following images.

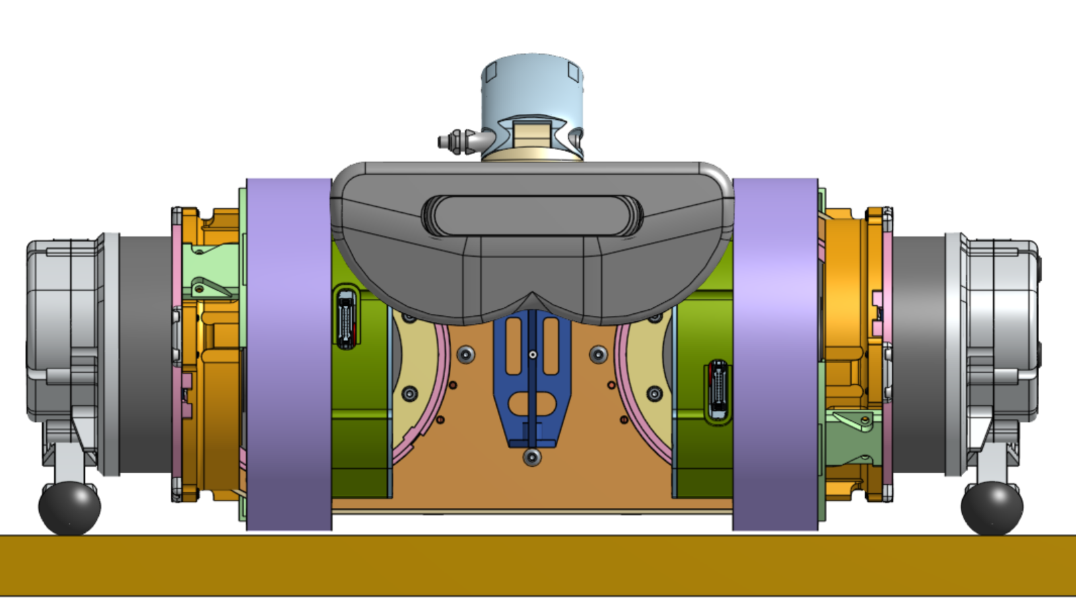
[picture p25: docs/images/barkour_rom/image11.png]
zero position front


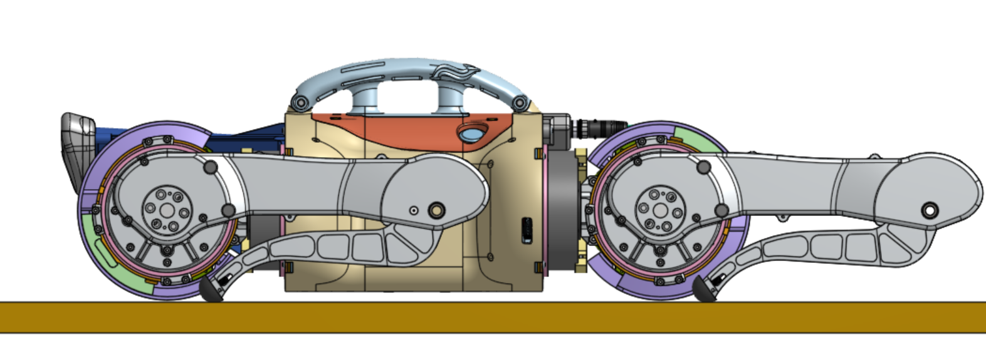
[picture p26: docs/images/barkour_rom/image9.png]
zero position side


## Barkour Robot Joint Directions

Each joint of the robot also has a defined convention for its positive and
negative rotation directions. The following images describe this convention.

### Abduction Lower Limit (-60 deg)

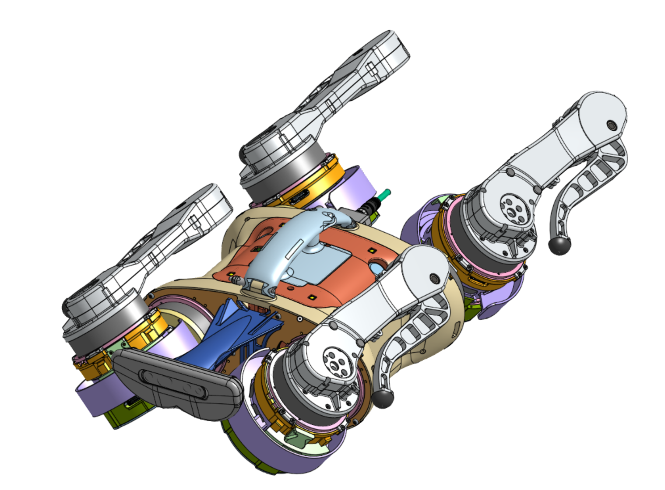
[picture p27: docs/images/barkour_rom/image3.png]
lower limit


### Abduction Upper Limit (60 deg)

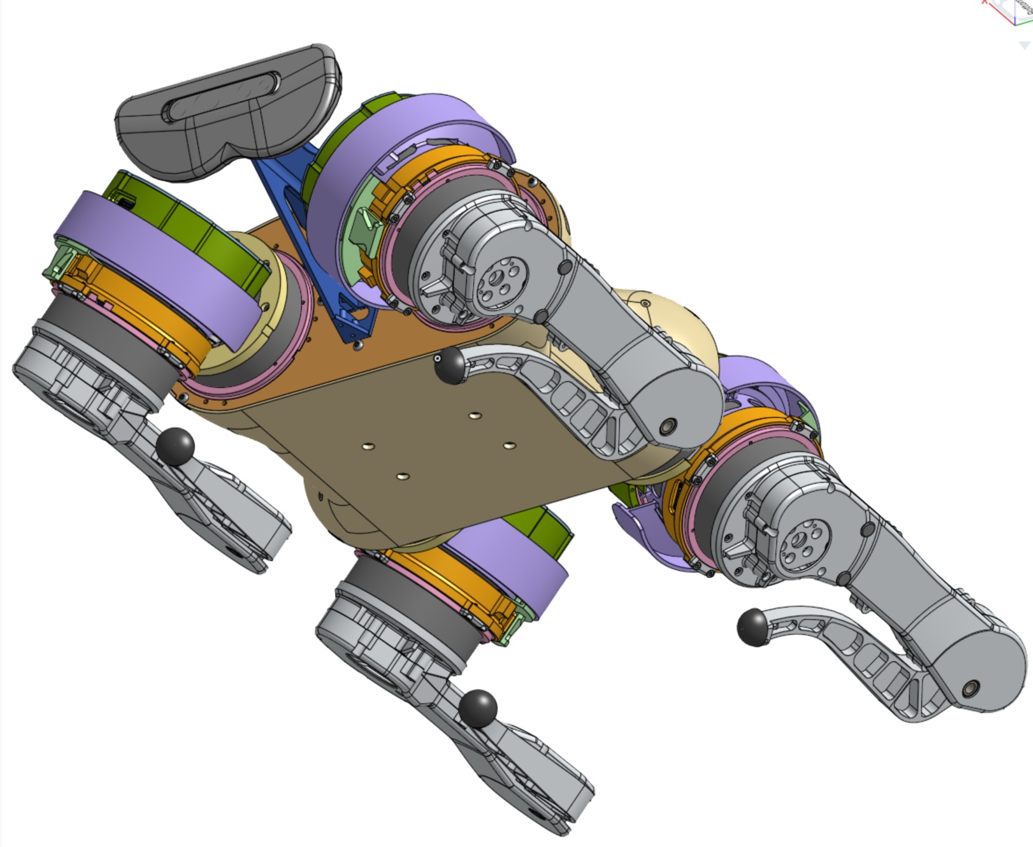
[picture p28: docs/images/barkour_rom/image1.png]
upper limit


### Hip & Knee

Arrows indicate positive direction.

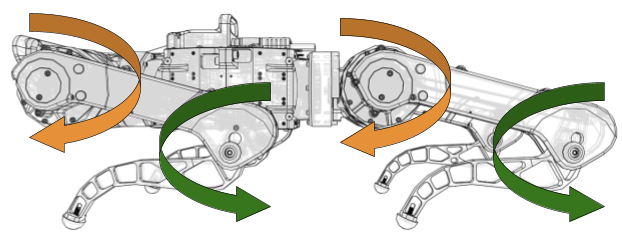
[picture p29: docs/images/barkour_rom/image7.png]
hip & knee 1


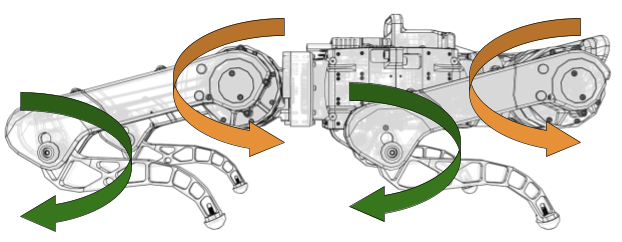
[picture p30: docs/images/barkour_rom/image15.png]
hip & knee 2


### Relative motor directions for Joints vs Motors

The following table lists the relative signs of the motor and joint rotation for
each joint of the robot. For joints with sign +1, the joint rotation direction
coincides with the motor rotation direction, whereas for joints with sign -1,
the two directions are opposite.

Robot Joint Leg Order | Robot Joint Order | joint_sign | Name
:-------------------: | :---------------: | :--------: | -----------------------
0                     | 0                 | +1         | "abduction_front_left"
                      | 1                 | +1         | "hip_front_left"
                      | 2                 | -1         | "knee_front_left"
1                     | 3                 | -1         | "abduction_hind_left"
                      | 4                 | +1         | "hip_hind_left"
                      | 5                 | -1         | "knee_hind_left"
2                     | 6                 | -1         | "abduction_front_right"
                      | 7                 | -1         | "hip_front_right"
                      | 8                 | +1         | "knee_front_right"
3                     | 9                 | +1         | "abduction_hind_right"
                      | 10                | -1         | "hip_hind_right"
                      | 11                | +1         | "knee_hind_right"

### Hip Range of Motion (-88.447; 173.557)

In the current version, the Range of Motion (ROM) of the hip is the same between
the front and hind legs.

hip rom 1

hip rom 2

### Knee Range of Motion (0; 140 deg)

knee rom 3

### Summary Table

Front Left | Hind Left | Front Right | Hind Right | Range
:--------: | :-------: | :---------: | :--------: | --------------------------
Abduction  | Abduction | Abduction   | Abduction  | -60 deg to +60 deg
Hip        | Hip       | Hip         | Hip        | -88.447 deg to 173.553 deg
Knee       | Knee      | Knee        | Knee       | 0 deg to 140 deg

## Barkour Robot Joint Position Calibration

As the encoder magnet cannot reliably be placed in a known orientation with
respect to the output shaft for each motor, we require a calibration routine in
order to calculate the correct joint position of the robot at any given time.

The calibration procedure needs to be run just once for each motor on the robot,
and is as follows. The joint is moved to the endstop at the negative end of its
range, that is:

*   Legs fully outwards for the abduction joints

*   Upper legs fully “backward” for the hip joints

*   Lower legs fully “closed” for the knee joints

At this joint position, a command is given to the firmware to store the current
encoder reading in EEPROM and use it as a zero offset when reporting positions
over the EtherCAT bus. See the [firmware documentation](firmware.md) for
instructions on how to send this command.

This means that once this calibration has been completed, the joint positions
can be calculated by:

```
joint_position = relative_motor_direction * motor_position + endstop_offset_from_zero
```

Where the endstop offsets from zero are given by the negative range limit for
each joint.

Front Left | Hind Left | Front Right | Hind Right | Endstop offset from zero
:--------: | :-------: | :---------: | :--------: | ------------------------
Abduction  | Abduction | Abduction   | Abduction  | -60 deg
Hip        | Hip       | Hip         | Hip        | -88.447g
Knee       | Knee      | Knee        | Knee       | 0 deg

### Turn-Count Initialization Strategies

In addition to the procedure described here, since the encoder is single-turn
only and is mounted on the input side of the actuator gearbox, there is a
further homing step required to correctly initialize the turn count each time
the robot starts up. This means that the effective zero offsets used differ from
those listed by some multiple of 360 degrees / gear ratio = 40 degrees.

There are multiple possible strategies for initializing the turn count to the
correct value and the software setup has been designed to allow simple swapping
in and out of different strategies:

1.  Nearest Zero Turn-Count Initialization

    If it is known that the robot has been started with its joints within +/-
    (pi / gear ratio) radians from the correct starting position, using the
    saved offsets it's possible to set the correct zero position for the joints.
    The precondition is easy to verify visually, but if the robot is not near
    the zero position and the user wants to start it, they will need to manually
    intervene and move the joints back to zero.

1.  IMU-based Turn-Count Initialization

    Each of the motor drivers has an on-board IMU on the stator side of the
    motor. This means that by comparing the abduction and hip IMUs, the
    abduction angle may be deduced, and by comparing the hip and knee IMUs, the
    hip angle may be deduced. By combining this with the saved motor offsets,
    the IMUs only need to be accurate enough to deduce the joint angles to
    within +/- (pi / gear ratio) radians, so this strategy should work well,
    with the following caveats:

    *   It cannot work for the knee joint, as there is no IMU on the rotor side
        of the knee.

    *   Due to close proximity with the motor magnets, the IMU magnetometer is
        unlikely to work well, so only the gravity vector can be reliably used
        to detect the joint angle. This should work as long as the joint axis is
        not too close to the gravity direction, but will not give usable results
        if these two axes are aligned.

1.  Endstop Homing

    There's also the option to move the joints to a chosen endstop to find the
    zero position. The downside is that depending on the configuration of the
    robot, it may not be able to freely move its joints to the endstop, or doing
    so could have unintended consequences such as flipping the robot over.

## Orientation (Roll, Pitch, Yaw) and Coordinate Frame

We use the
[Land Vehicle conventions](https://en.wikipedia.org/wiki/Axes_conventions).

coordinate conventions

ENU (East North Up) right handed coordinate frame convention with the X (East)
axis along the body of the robot as shown below.

ENU coord

### Base Frame

Origin on the mid plane of the abduction motors (and centred width and length)
between said joints. Orientation with X-forward, Y-left, Z-upwards (i.e. the
aforementioned convention for orientation). IMU and other observations
are to be transformed to this frame. Projection of the frame is printed on the
chassis as shown below.

chassis frame

## Actuated Head

actuated head rom

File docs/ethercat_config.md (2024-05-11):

# EtherCAT Configuration (Host Side)

[TOC]

This document explains how to install and troubleshoot the EtherCAT bus.

## EtherCAT Drivers

The EtherLab library must be installed on the computer connected to the EtherCAT
bus, which is typically on the robot's onboard computer. We use EtherLab, which
is a Linux kernel-based library that implements an EtherCAT host. See
[here](https://www.etherlab.org/en/ethercat/index.php) for details.

### EtherLab Installation Instructions

The following outlines how to install the EtherLab host from source. For more
comprehensive instructions, see the
[EtherLab documentation](https://www.etherlab.org/download/ethercat/ethercat-1.5.2.pdf).

1.  Install the required libraries and kernel headers.

    ```
    sudo apt install autoconf libtool build-essential git pkg-config vim ethtool cpuset
    sudo apt-get install linux-headers-`uname -r`
    ```

1.  Clone the repository and enter the directory.

    ```
    git clone https://gitlab.com/etherlab.org/ethercat.git
    cd ethercat
    ```

1.  Check out the stable version.

    ```
    git checkout stable-1.5
    ```

1.  Bootstrap and configure the toolchain; disable the `8139too` driver, which
    is not required/supported, and enable the generic driver.

    ```
    ./bootstrap
    ./configure --disable-8139too --enable-generic
    ```

    `bootstrap` might give an error, asking you to run `autoupdate`. In this
    case, you should run `autoupdate` followed by `bootstrap` again.

1.  Build the userland library and kernel modules.

    ```
    make && make modules
    ```

1.  Install the user land library and kernel modules.

    ```
    sudo make install && sudo make modules_install
    sudo depmod
    ```

1.  Create symlinks for the EtherCAT configuration. The current version of
    EtherLab also tries to use `sh`, which is problematic on many machines. We
    use `bash` instead:

    ```
    sudo mkdir -p /etc/sysconfig/
    sudo ln -s /usr/local/etc/init.d/ethercat /etc/init.d/ethercat
    sudo cp /usr/local/etc/sysconfig/ethercat /etc/sysconfig/ethercat
    sed '1 s/^.*$/#!\/bin\/bash/' /etc/init.d/ethercat  | sudo tee /etc/init.d/ethercat > /dev/null
    ```

1.  Edit the configuration file to point it to the correct NIC and enable the
    generic driver module. First, find the MAC address of the NIC you would like
    to use for EtherCAT, e.g., using `ip link`. Then with your favourite editor,
    edit the file `/etc/sysconfig/ethercat` to set up the configuration. For
    example, if the NIC you're using has MAC address `aa:bb:cc:dd:ee:ff`, edit
    the file to look like:

    ```
    ...

    # Main Ethernet devices
    ...

    MASTER0_DEVICE="aa:bb:cc:dd:ee:ff"
    #MASTER1_DEVICE=""

    ...

    # Backup Ethernet devices

    ...

    #MASTER0_BACKUP=""

    ...

    # Ethernet driver modules to use for EtherCAT operation

    ...

    DEVICE_MODULES="generic"

    ```

1.  (Re)start the host. This reloads the kernel modules and starts the kernel
    threads that process EtherCAT data.

    ```
    sudo /etc/init.d/ethercat restart
    ```

    Tip: If you get an error like `FATAL: Module ec_master not found in
    directory /lib/modules/5.13.0-44-generic`, your kernel has likely been
    updated since the last install and the kernel module version no longer
    matches your kernel version. Delete the `ethercat` folder, go back to step 1
    and try again. If the problem persists, reboot and try running `sudo
    /etc/init.d/ethercat restart` once more.

1.  Allow non-root access to the EtherCAT port:

    ```
    sudo sh -c "echo 'KERNEL==\"EtherCAT[0-9]*\", MODE=\"0666\"' > /etc/udev/rules.d/99-EtherCAT.rules"
    sudo udevadm control --reload-rules
    sudo udevadm trigger
    ```

To check if the install has worked, you should be able to see a summary of the
host status by running `ethercat master`, which gives an output like:

```
$ ethercat master

Master0
  Phase: Idle
  Active: no
  Slaves: 0
  Ethernet devices:
    Main: aa:bb:cc:dd:ee:ff (attached)
      Link: UP
      Tx frames:   0
      Tx bytes:    0
      Rx frames:   0
      Rx bytes:    0
      Tx errors:   0
      Tx frame rate [1/s]:      0      0      0
      Tx rate [KByte/s]:      0.0    0.0    0.0
      Rx frame rate [1/s]:      0      0      0
      Rx rate [KByte/s]:      0.0    0.0    0.0
    Common:
      Tx frames:   388038
      Tx bytes:    65393294
      Rx frames:   388038
      Rx bytes:    65393294
      Lost frames: 0
      Tx frame rate [1/s]:      0      0      0
      Tx rate [KByte/s]:      0.0    0.0    0.1
      Rx frame rate [1/s]:      0      0      0
      Rx rate [KByte/s]:      0.0    0.0    0.1
      Loss rate [1/s]:          0      0      0
      Frame loss [%]:         0.0  100.0    1.7
  Distributed clocks:
    Reference clock:   None
    DC reference time: 0
    Application time:  0
                       2000-01-01 00:00:00.000000000
```

If you attach a motor module to the EtherCAT bus and power it on, then you can
also check the output of `ethercat slaves`, which should show something like
this:

```
$ ethercat slaves
0  1:0  PREOP  +  Cortes
```

## Configuring EtherCAT Devices (Motor Drivers) On the Bus

When installing new motor drivers, it's important to assign the correct EtherCAT
device alias to each driver to ensure the correct joint order in software. In
our typical configuration, the physical EtherCAT motor order is different from
the logical one for historical reasons. The physical to logical mapping is shown
below.

| **Joint | **Position on ECAT | **ECAT device | **Joint name**          |
: index** : bus**              : alias**       :                         :
| :-----: | :----------------: | :-----------: | :---------------------: |
| 0       | 0                  | 1             | abduction\_front\_left  |
| 1       | 1                  | 2             | hip\_front\_left        |
| 2       | 2                  | 3             | knee\_front\_left       |
| 3       | 9                  | 4             | abduction\_hind\_left   |
| 4       | 10                 | 5             | hip\_hind\_left         |
| 5       | 11                 | 6             | knee\_hind\_left        |
| 6       | 3                  | 7             | abduction\_front\_right |
| 7       | 4                  | 8             | hip\_front\_right       |
| 8       | 5                  | 9             | knee\_front\_right      |
| 9       | 6                  | 10            | abduction\_hind\_right  |
| 10      | 7                  | 11            | hip\_hind\_right        |
| 11      | 8                  | 12            | knee\_hind\_right       |

Note: Bus positions use 0-based indexing (0-11), whereas aliases use 1-based
indexing (1-12) 🤷.

Use the `ethercat alias` command to set the correct device aliases:

```bash
ethercat alias -p0 1
ethercat alias -p1 2
ethercat alias -p2 3
ethercat alias -p9 4
ethercat alias -p10 5
ethercat alias -p11 6
ethercat alias -p3 7
ethercat alias -p4 8
ethercat alias -p5 9
ethercat alias -p6 10
ethercat alias -p7 11
ethercat alias -p8 12
```

## Flashing New Firmware

See [this page](firmware.md) for instructions.

## Restarting Motor Drivers Via EtherCAT

Important: This feature is only supported on the Holberton version of
the motor drivers. If you run this tool on the Gebru + Cortes
version, the motor driver will be held in reset until you (manually) power cycle
the motors.

It is possible to send a sequence of low-level EtherCAT commands to reset motor
drivers on the bus. This will toggle the reset pins on both the EtherCAT chip
(Trinamic) and the main microcontroller (STM32H7). This is equivalent to
pressing the reset button (power cycle) on the board or the Mataric debugger.

This is implemented as a standalone binary in the
[reset_motor_driver](../actuator/ethercat_host/reset_motor_driver.cc) example.

This script uses the [SOEM](https://github.com/OpenEtherCATsociety/SOEM) library
instead of EtherLab in order to send individual EtherCAT frames. To run it on
the robot, stop the Etherlab kernel module, run the script, then restart the
Etherlab kernel module. The `reset_motor_driver` binary should have permission
to access raw sockets.

```bash
sudo setcap CAP_NET_RAW+pe reset_motor_driver
sudo systemctl stop ethercat
./reset_motor_driver --alsologtostderr --ethercat_interface=enx7cc2c6473b62
sudo systemctl start ethercat
```

## Common Error Conditions

Below are details of some common error messages that may be encountered when
using the hardware.

**Boards come up in error state, for example: `(3 7:0 INIT E Cortes)`**

When running `ethercat slaves`, one or more motor drivers show up as faulted:

```
3   7:0  INIT   E  Cortes
```

or have incorrect information:

```
11   6:0  INIT   +  0x00600613:0x00001000
```

This usually indicates that either the EEPROM on the EtherCAT chip or the flash
memory on the microcontroller is corrupted. We have noticed the former in case
of brownout conditions. See the
[actuator assembly and setup](actuator_assembly_and_setup.md) documentation to
reflash the EEPROM (SII) and the [firmware](firmware.md) page to reflash the
embedded software.

**Unexpected working counter received from the EtherCAT bus**

When an EtherCAT frame is sent around the bus by the host, each device (e.g. a
motor driver) on the bus increments the working counter of each datagram in the
frame that it interacts with. The increment amounts depend on the action that
the device is commanded to carry out, but in the usual case (device is commanded
to read and write from the datagram), the working counter is incremented by +1
for a successful read and by +2 for a successful write. Hence, the working
counter should be equal to 3 times the number of devices on the bus. A mismatch
indicates a communication failure with at least 1 device on the bus.

There are various reasons this can happen, including:

-   A lost or unreliable physical connection to a device
-   Incorrect behaviour of device firmware
-   Devices not having enough time to process datagrams, due to an overly high
    EtherCAT cycle frequency or excessive jitter on the bus

Depending on the characteristics of the host system (e.g. if it's running an RT
kernel, or CPU isolation for the userland process), some working counter errors
may be expected due to jitter.

**More than one device found on EtherCAT bus matching device address**

The most likely cause of this is that a device alias is incorrectly configured,
causing two devices on the bus to have the same alias. This might occur after
swapping a motor or reflashing the SII.

You can use the `ethercat slaves` command on the computer connected to the
EtherCAT bus to verify the device order. Once you identify the incorrectly
configured device, use the `ethercat alias` command to fix it.

Example incorrect configuration, followed by a fix:

```
barkour@barkour:~$ ethercat slaves
 0   1:0  PREOP  +  Cortes
 1   2:0  PREOP  +  Cortes
 2   3:0  PREOP  +  Cortes
 3   7:0  PREOP  +  Cortes
 4   8:0  PREOP  +  Cortes
 5   9:0  PREOP  +  Cortes
 6  10:0  PREOP  +  Cortes
 7  11:0  PREOP  +  Cortes
 8  12:0  PREOP  +  Cortes
 9   4:0  PREOP  +  Cortes
10   5:0  PREOP  +  Cortes
11   1:0  PREOP  +  Cortes  # Duplicate alias 1 (should be alias 6).
barkour@barkour:~$ ethercat alias -p11 6  # Set motor driver at position 11 to use alias 6
barkour@barkour:~$ ethercat slaves
 0   1:0  PREOP  +  Cortes
 1   2:0  PREOP  +  Cortes
 2   3:0  PREOP  +  Cortes
 3   7:0  PREOP  +  Cortes
 4   8:0  PREOP  +  Cortes
 5   9:0  PREOP  +  Cortes
 6  10:0  PREOP  +  Cortes
 7  11:0  PREOP  +  Cortes
 8  12:0  PREOP  +  Cortes
 9   4:0  PREOP  +  Cortes
10   5:0  PREOP  +  Cortes
11   6:0  PREOP  +  Cortes  # Correct alias.
```

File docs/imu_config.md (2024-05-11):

# Onboard IMU Configuration

This page describes the steps required to configure the onboard IMUs. We use the
3DM-CV7-AHRS
([product specs](https://www.microstrain.com/inertial-sensors/3dmcv7-ahrs)) IMU
from MicroStrain.

3DM-CV7-AHRS

### Configuration steps for a new device.

1.  Get a brand-new IMU and an
    [FTDI serial device (SparkFun FTDI Basic Breakout - 5V)](https://www.sparkfun.com/products/9716).
    Connect the IMU to a Windows PC. To do so, plug the IMU into a Hamilton
    board and plug in the FTDI cable (or use a breakout board provided by
    Microstrain).

2.  Open the [SensorConnect](https://www.microstrain.com/software/sensorconnect)
    app and go to the Device tab on top left. Click on "+Add Device" button on
    the bottom left. The connection should be via "Serial", at a COM port that
    is available (corresponding to the FTDI device port) and (initially) at a
    baud rate 115200 bps. Hit "Add Device" and you should see the device added
    on the left pane. 3DMCV7-AHRS
    Clicking on the device name will bring up the dashboard shown:

    dashboard

3.  [Optional] Update the IMU firmware. The 3DM-CV7-AHRS firmware has a bug that
    causes the quaternions to sporadically return NaNs. If you encounter this
    issue, contact Microstrain for updated firmware.

4.  Click on "UART baud rate" and change baud rate to 921600.

    baud_rate

5.  Save the current settings on to the device by clicking "Save/Load Settings",
    and then "Save as Startup Settings".
    save_as_startup_settings

    Make sure that the "Stream Data on Startup" button is **unticked**. This
    prevents the IMU from streaming data immediately on startup (data stream
    will be initiated by the NUC during normal operation).

    uncheck_startup_stream

6.  At this point it is helpful to re-add the device following step 2, this time
    configured at the new 921600 baud rate. If the change in baud rate is not
    saved and the device not re-added immediately, the baud rate can revert
    to 115200.

7.  On the new device, click on "configure" and select "Enable North
    Compensation" tickbox under Complementary Filter Settings. Apply the
    configuration.
    north_compensation

8.  Repeat step 4 to save the current settings on to the device by clicking
    "Save/Load Settings", and then "Save as Startup Settings". "Stream Data on
    Startup" should again be unticked.

9.  Check that the IMU is working properly. Click on "Sampling" and in the IMU
    Channel field, add "Accelerometer vector" and "Gyroscope vector" fields. if
    there is an error message in red, hit "Fix". Hit "Start on the lower right
    as shown:

    test_sampling

10. Go to the "Data" tab in the top left. In the "Channels" pane, the active
    device should have a green dot next to it indicating that it is streaming
    data. Click "Add Widget" on the top of the right pane and select "time
    series".

    add_widget

11. Select a few active channels on the left (with a green dot) to add to the
    widget. The widget should be displaying those channels now. Shake and tap on
    the IMU to see the change in the signals. Hopefully nothing looks odd.

    check_data

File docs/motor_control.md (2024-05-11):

# Motor Control

We provide a C++ example to connect to the motors via EtherCAT and send
torque/position commands to the actuators.

The implementation can be found at `actuator/ethercat_host/ethercat_example.cc`.

Important: This example does not include safety features, so make sure to refine
it before using it in a real system. Please also review the
[basic robot instructions](getting_started.md).

## Running the EtherCAT Host Side Example

Note: To connect to hardware, make sure the Etherlab kernel module has been
installed and the motor drivers are showing up on the bus. See
[EtherCAT config](ethercat_config.md) for instructions. Make sure you are using
the same version for the kernel module and the user mode code below.

Note: Instructions to compile and flash the firmware can be found
[here](firmware.md).

Note: We are using [Bazel](https://bazel.build) as the build system. The
instructions below were tested with `bazel 7.1.2` on Debian and Ubuntu.

As we are using Etherlab to communicate via the EtherCAT bus, we clone the
Etherlab repo and configure it (only needed once):

```bash
cd actuator/ethercat_host

# Download and configure the EtherLab library.
sudo apt install autoconf libtool build-essential git pkg-config vim ethtool cpuset
sudo apt-get install linux-headers-`uname -r`
rm -Rf etherlab
git clone https://gitlab.com/etherlab.org/ethercat.git etherlab
cd etherlab
git checkout stable-1.5
./bootstrap
# We run ./configure to generate the config.h file.
./configure --disable-8139too --enable-generic
```

Now you can compile the example and run it:

```bash
# Compile and run the example
cd ../..
bazel build --cxxopt='-std=c++17' -c opt ethercat_host:ethercat_example
bazel-bin/ethercat_host/ethercat_example --stderrthreshold=0
```

The expected behavior is that all actuators are held in place and that one joint
slowly wiggles (the actuator with device alias 1).

To give the example a try without hardware, just add the `fake_ethercat_host`
flag:

```bash
bazel-bin/ethercat_host/ethercat_example --stderrthreshold=0 --fake_ethercat_host
```

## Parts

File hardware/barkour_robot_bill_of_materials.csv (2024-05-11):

 | No. of Robots : 1
Item No. | PART | Specification/ Unit | TYPE | MANUFACTURER | Mfg. Product No. / SKU | Source | Total Quantity Required | Additional Notes
Motor Module
1 | AK80-9 Motors | 48V, 9Nm, 390RPM | Electronics | TMotor |  | T-Motor | 12
2 | Gebru | see schematic | Electronics |  |  | Custom Order | 12
3 | Cortes | see schematic | Electronics |  |  | Custom Order | 12
4 | Ada | see schematic | Electronics |  |  | Custom Order | 12
5 | Heat Sinks | Aluminum 7075 | Machined |  |  | Custom Order | 12
6 | Ada Separator | Acetal Copolymer (POM-C) | Machined |  |  | Custom Order | 12
7 | Thermal Pad | Silicone Elastomer, 2mm thickness | Other | DigiKey | 5595S-210MMX300MM | DigiKey | 1 | Cut to size.
8 | Thermal Paste | 0.864 w/m-k | Other | McMaster | 1688N12 | McMaster | 1
Tri-Motor
9 | Hip Bracket | Aluminum 7075 | Machined |  |  | Custom Order | 4
10 | Knee Bracket (Left) | Aluminum 7075 | Machined |  |  | Custom Order | 2
11 | Knee Bracket (Right) | Aluminum 7075 | Machined |  |  | Custom Order | 2
12 | Abduction HardStop | Aluminum 7075 | Machined |  |  | Custom Order | 4
13 | Hip HardStop | Aluminum 7075 | Machined |  |  | Custom Order | 4
14 | Cleats | Stainless Steel 17-4 PH | Machined |  |  | Custom Order | 48
15 | Hip Cover | HP PA 11 (nylon) | 3D Printed |  |  | Custom Order | 4
16 | Hip Cover Clamps | HP PA 11 (nylon) | 3D Printed |  |  | Custom Order | 8
17 | Knee Cable Cover Top | HP PA 11 (nylon) | 3D Printed |  |  | Custom Order | 4
18 | Knee Cable Cover Bottom | HP PA 11 (nylon) | 3D Printed |  |  | Custom Order | 4
19 | Thrust Bushing | PTFE | Machined |  |  | Custom Order | 4
20 | Wrap-Around Sleeving | 1/2" ID, 10ft cut to length | Hardware | McMaster | 1459T818 | McMaster | 1
21 | Hip-Power-Distro | See cable drawing | Wiring |  |  | Custom Order | 4
22 | Fei-Fei_to_A+H_RE | See cable drawing | Wiring |  |  | Custom Order | 2
23 | Fei-Fei_to_A+H_FR | See cable drawing | Wiring |  |  | Custom Order | 2
24 | NUC_ECAT_TORSO | See cable drawing | Wiring |  |  | Custom Order | 1
25 | A2H_ECAT | See cable drawing | Wiring |  |  | Custom Order | 4
26 | H2K_ECAT | See cable drawing | Wiring |  |  | Custom Order | 4
27 | K2H_COVER_ECAT | See cable drawing | Wiring |  |  | Custom Order | 4
28 | Hip-Return-SS-Ecat | See cable drawing | Wiring |  |  | Custom Order | 2
29 | Hip_Return_OS_ECAT | See cable drawing | Wiring |  |  | Custom Order | 2
30 | Hip_Return_to_Rus_STO_TORSO | See cable drawing | Wiring |  |  | Custom Order | 1
31 | Hip_Return_To_RUS_STO_DFB | See cable drawing | Wiring |  |  | Custom Order | 1
Legs
32 | Inner Upper Leg (Left) | Aluminum 7075 | Machined |  |  | Custom Order | 2
33 | Outer Upper Leg (Left) | Aluminum 7075 | Machined |  |  | Custom Order | 2
34 | Inner Upper Leg (Right) | Aluminum 7075 | Machined |  |  | Custom Order | 2
35 | Outer Upper Leg (Right) | Aluminum 7075 | Machined |  |  | Custom Order | 2
36 | Crank (Left) | Aluminum 7075 | Machined |  |  | Custom Order | 2
37 | Crank (Right) | Aluminum 7075 | Machined |  |  | Custom Order | 2
38 | Linkage | Aluminum 7075 | Machined |  |  | Custom Order | 4
39 | Knee Half Pin Clearance | Stainless Steel 17-4 | Machined |  |  | Custom Order | 4
40 | Knee Half Pin Tapped | Stainless Steel 17-4 | Machined |  |  | Custom Order | 4
41 | Linkage Half Pin Clearance | Stainless Steel 17-4 | Machined |  |  | Custom Order | 4
42 | Linkage Half Pin Tapped | Stainless Steel 17-4 | Machined |  |  | Custom Order | 4
43 | Lower Leg | PEEK (Polyether Ether Ketone) | Machined |  |  | Custom Order | 4
44 | Leg Bumper | Silicone Rubber | 3D Printed |  |  | Custom Order | 4
45 | Knee Bumper | Silicone Rubber | 3D Printed |  |  | Custom Order | 4
46 | Foot | Fluoroelastomer (FKM) | 3D Printed |  |  | Custom Order | 4
47 | Flanged Ultra-Thin Ball Bearing | Open, 12 mm ID, 21mm OD, 5mm wide | Hardware | McMaster | 4390N122 | McMaster | 8
48 | Stainless Steel Ball Bearing | 6mm ID, 12mm OD, 4mm wide | Hardware | McMaster | 7804K112 | McMaster | 16
Deep Fry Basket
49 | DFB | HP PA 11 (nylon) | 3D Printed |  |  | Custom Order | 1
50 | Antenna Panel | HP PA 11 (nylon) | 3D Printed |  |  | Custom Order | 1
51 | USB Panel | HP PA 11 (nylon) | 3D Printed |  |  | Custom Order | 1
52 | Battery Holder | HP PA 11 (nylon) | 3D Printed |  |  | Custom Order | 1
53 | Anode/Cathode Electrodes | Copper C101, Nickel plating | Machined |  |  | Custom Order | 2
54 | U-Shaped Electrode | Copper C101, Nickel plating | Machined |  |  | Custom Order | 1
55 | Rus HeatSink | Copper C101, Nickel plating | Machined |  |  | Custom Order | 1
56 | RUS | see schematic | Electronics |  |  | Custom Order | 1
57 | Hopper | see schematic | Electronics |  |  | Custom Order | 1
58 | Remote E-stop Transceiver Module | RF TXRX 802.15.4 U.FL SMD, 2.4GHz | Electronics | Digi | XB3-24Z8UM | DigiKey | 2
59 | Hamilton | see schematic | Electronics |  |  | Custom Order | 1
60 | NUC RAM | RAM Kingston FURY 64GB DDR4 3200MHz | Electronics | Kingston Technologies | ‎KF432S20IBK2/64 | Amazon | 2
61 | NUC SSD | 2048G NVMe M.2 SSD | Electronics | Kingston Technologies | ‎SKC3000D/2048G | Amazon | 1
62 | NUC WiFi Card | WiFi 6, 2400 Mbps, BT 5.2 | Electronics | NICGIGA | AX201 | Amazon | 1
63 | Ethernet Adapter | USB 3.0 male A to RJ45 female, 1000 Mbps | Electronics | TP-Link | UE306 | Amazon | 1
64 | Intel NUC 11 Intel Core i7 4.4 GHz | Intel NUC 11 Intel Core i7 4.4 GHz | Electronics | Intel | BNUC11TNBV70000 | Mouser | 1
65 | IMU | UART, USB | Electronics | MicroStrain | 3DM-CV7-AHRS | Mouser | 1
66 | WiFi Antenna | RF ANT 2.4Ghz/5.5Ghz | Electronics | Abracon LLC | PRO-EX-285 | DigiKey | 2
67 | Cable Assembly Coaxial SMA to IPEX MHF4 | 152.00mm | Electronics | Adam Tech | CA-DKCA1-152L0-AJI5 | DigiKey | 2
68 | On-robot E-stop Antenna | RF ANT 2.4Ghz | Electronics | OTS (OTHER) | PRO-EX-296 | DigiKey | 1
69 | DeWalt DCB546(606) Battery | 6AH, 60V | Electronics | DeWalt | DCB606 | Home Depot | 2
70 | DeWalt Battery Handles | 1 x 17",tensile strength > 2.5lbs | Hardware | ULINE | S-6782 | Uline | 1
71 | RGB Fan | 40mm, 24V | Electronics | WINSINN | RGBFAN301024VH | Amazon | 2
72 | 2POS molex connector | Receptable, 2.5mm nano fit | Electronics | Molex | 1053071202 | Digikey | 2
73 | nano-fit crimp | 24-26AWG, female | Electronics | Molex | 1053001200 | Digikey | 2
74 | M12 Ethernet Cable (Internal) | See cable drawing (34_Internal_Ethernet_Access) | Wiring |  | 1440591 | Mouser | 1 | Cut to length.
75 | Pheonix Contact M12 Ethernet Cable (External) | 10m | Wiring | PC | 1080737 | Mouser | 1
76 | USB C to C Panel Mount Cable | See cable drawing | Wiring |  |  | Custom Order | 1
77 | USB A to C Panel Mount Cable | See cable drawing | Wiring |  |  | Custom Order | 1
78 | NUC to RUS Cable | MICRO-FIT3.0 R-R 4 CIRCUIT 150MM | Wiring | Mouser | 2147552041 | Mouser | 1
79 | NUC Internal USB for IMU | 1.25mm 1x4 Pin each side | Wiring | Gorite | INTL-4P4P-6IN | Micro SATA Cables | 1
80 | Rus_Power_In | See cable drawing | Wiring |  |  | Custom Order | 1
81 | STO Switch | See cable drawing | Wiring |  |  | Custom Order | 1
82 | Power Switch | See cable drawing | Wiring |  |  | Custom Order | 1
83 | NUC_ECAT_DFB | See cable drawing | Wiring |  |  | Custom Order | 1
84 | Rus_to_Hopper | See cable drawing | Wiring |  |  | Custom Order | 1
85 | Rus_to_Fei-Fei | See cable drawing | Wiring |  |  | Custom Order | 1
Torso
86 | Combined Face plate | Anodized Aluminum 7075 | Machined |  |  | Custom Order | 2
87 | Chassis (Torso) | HP PA 11 (nylon) | 3D Printed |  |  | Custom Order | 1
88 | Handle | HP PA 11 (nylon) | 3D Printed |  |  | Custom Order | 1
89 | Camera Mount | HP PA 11 (nylon) | 3D Printed |  |  | Custom Order | 1
90 | Abduction Grommet Top | HP PA 11 (nylon) | 3D Printed |  |  | Custom Order | 4
91 | Abduction Grommet Bottom | HP PA 11 (nylon) | 3D Printed |  |  | Custom Order | 4
92 | Padding (FR/RL) | Silicone Rubber | 3D Printed |  |  | Custom Order | 2
93 | Padding (FL/RR) | Silicone Rubber | 3D Printed |  |  | Custom Order | 2
94 | Holberton | see schematic | Electronics |  |  | Custom Order | 1
95 | Fei-Fei | see schematic | Electronics |  |  | Custom Order | 1
96 | Narrow-Grip Locking Quick-Release Pin | 6mm Diameter, 25mm Usable Length | Hardware | McMaster | 93871A110 | McMaster | 1
Remote
97 | WSTO Cover Base | HP PA 11 (nylon) | 3D Printed |  |  | Custom Order | 1
98 | WSTO Cover Lid | HP PA 11 (nylon) | 3D Printed |  |  | Custom Order | 1
99 | Grace | see schematic | Electronics |  |  | Custom Order | 1
100 | Remote E-stop Portable Power Bank | Input: 5V / 2.4A, output: 5V / 2.4A | Electronics | TNTOR | WT-H369 | Amazon | 1
101 | Remote E-stop Power Bank Cable | USB A 2.0 to USB C Up Angled, 13cm, flat slim | Electronics | Xiwai | UC-096-UP-0.13M-XY | Amazon | 1
102 | Remote E-stop Antenna | 2.4GHz Whip, Straight RF. Panel Mount | Electronics | Digi | A24-HABUF-P5I-ND | Digikey | 1
103 | Remote E-stop Button | SW ESTOP 3A 125V 40mm Mushrom | Electronics | IDEC | XA1E-BV404-R | DigiKey | 1
104 | XBox Controller |  | Electronics | Microsoft | QAU-00021 | Amazon | 1
105 | Mataric Debug Board | see schematic | Electronics |  |  | Custom Order | 1
106 | J-Link Pro (cables included) |  | Electronics | Segger | 8.12.00 | Segger | 1
107 | Samtec 20 Position Cable Assembly | Socket to Socket, 1.27mm | Electronics | Samtec Inc. | SFSD-10-28-G-10.00-D-NDX | Digikey | 1
Static Head
108 | Head (Real Sense Camera Cover) | HP PA 11 (nylon) | 3D Printed |  |  | Custom Order | 1
109 | Neck | HP PA 11 (nylon) | 3D Printed |  |  | Custom Order | 1
110 | Real Sense Depth Camera D435i | 90 fps, RGB | Electronics | Intel | 82635D435IDK5P | Mouser | 1
111 | USB C to C for Realsense Camera | See cable drawing | Wiring |  |  | Custom Order | 1
112 | OAK-FFC Platform (Luxonis Board) |  | Electronics | Luxonis | OAK-FFC 4P | Luxonis | 1
113 | OAK-FFC Camera Module | OV9782, 1280 x 800 at 120 FPS | Electronics | Luxonis | OAK-FFC-OV9782-M12 | Luxonis | 1
114 | OAK Lens | 1/2.3″, 2.72 mm | Electronics | ArduCam | M23272M14 (LN056) | Dlscorp | 1
115 | OAK FFC Cable | 25cm | Wiring | Luxonis | OAK-FFC-UC921-3 | Luxonis | 1
Actuated Head
116 | Jackson | see schematic | Electronics |  |  | Custom Order | 1
117 | Neck Base | Markforged Continous Fiberglass or Carbon | 3D Printed |  |  | Custom Order | 1
118 | Neck Base Cover | Markforged Continous Fiberglass or Carbon | 3D Printed |  |  | Custom Order | 1
119 | Bracket Stop Neck Pitch | SLS PA 11 0R 12 | 3D Printed |  |  | Custom Order | 1
120 | Neck Structure | Markforged Continous Fiberglass or Carbon | 3D Printed |  |  | Custom Order | 1
121 | Spring Mandrel | SLS PA 11 0R 12 | 3D Printed |  |  | Custom Order | 1
122 | Head Structure | Markforged Continous Fiberglass or Carbon | 3D Printed |  |  | Custom Order | 1
123 | Camera Bracket | Markforged Continous Fiberglass or Carbon | 3D Printed |  |  | Custom Order | 1
124 | Spacer Washer | SLS PA 11 0R 12 | 3D Printed |  |  | Custom Order | 1
125 | Jaw Upper Structure | SLS PA 11 0R 12 | 3D Printed |  |  | Custom Order | 1
126 | Jaw Lower Structure | SLS PA 11 0R 12 | 3D Printed |  |  | Custom Order | 1
127 | Neck (Right) | SLS PA 12 | 3D Printed |  |  | Custom Order | 1
128 | Neck (Left) | SLS PA 12 | 3D Printed |  |  | Custom Order | 1
129 | Head | SLS PA 12 | 3D Printed |  |  | Custom Order | 1
130 | Jaw Lower Outer | SLS PA 12 | 3D Printed |  |  | Custom Order | 1
131 | Bracket Stop Neck Pitch Upper | SLS PA 12 | 3D Printed |  |  | Custom Order | 1
132 | Flexible light pipe RGB | Cut length to 3" from connector end | Electronics | Bivar Inc. | SZ1-6.00-RGB-F4PD | Digikey | 1
133 | OAK-FFC Platform (Luxonis Board) |  | Electronics | Luxonis | A00470 | Luxonis | 1
134 | OAK-FFC Camera Module | OV9782, 1280 x 800 at 120 FPS | Electronics | Luxonis | OAK-FFC-OV9782-M12 | Luxonis | 2
135 | OAK Lens | 1/2.3″, 2.72 mm | Electronics | ArduCam | M23272M14 (LN056) | Dlscorp | 2
136 | OAK FFC Cable | 25cm | Wiring | Luxonis | OAK-FFC-UC921-3 | Luxonis | 3
137 | Dynamixel XH430-W350-T |  | Electronics | Robotis | XH430-W350-T | Robotis | 2
138 | Horn for XH430-W350-T |  | Hardware | Robotis | EPX430-BR101 | Robotis | 2
139 | Idler Bearing for XH430-W350-T |  | Hardware | Robotis | HN12-I101 | Robotis | 1
140 | Brass Screw-to-Expand Inserts for Plastic | M3 x 0.5 mm Thread, 4.8 mm Installed Length | Hardware | McMaster | 94510A030 | McMaster | 11 | Pack of 50
141 | Brass Tapered Heat-Set Inserts for Plastic | M3 x 0.5 mm Thread, 6.4 mm Installed Length | Hardware | McMaster | 94180A333 | McMaster | 25 | Pack of 100
142 | Shims (Head) | 20MM ID, 28MM OD | Hardware | McMaster | 90214A441 | McMaster | 2 | Pack of 5
143 | Oversized washer M2.5 | M2.5, 0.7-0.9 Thick, 2.7mm ID, 8mm OD | Hardware | McMaster | 91100A110 | McMaster | 4 | Pack of 100
144 | Wave Disc Spring (HEAD) | 0.012" Thick, 0.787" ID, 1.094" OD | Hardware | McMaster | 9714K18 | McMaster | 1 | Pack of 10
145 | Torsion Spring | 0.68" Length, 2" Leg Length, 0.659" ID, | Hardware | Century Spring | TO-5188L | Century Spring | 1
146 | Jumper Lead Socket to Socket | MINI SPOX 2.5 F-F 225MM 22 AWG B | Hardware | Molex | 2196761123 | Digikey | 6
147 | 3 Rectangular Connectors | CONN RCPT HSG 3POS 2.50mm | Hardware | JST Sales America Inc. | EHR-3 | Digikey | 4
148 | Socket Contact Crimp | CONN SOCKET 22-30AWG CRIMP TIN | Hardware | JST Sales America Inc. | SEH-001T-P0.6 | Digikey
149 | Lockring | M12X0.5 | Hardware | Basler Inc. | 2000035198 | Digikey | 4
150 | USB A to C for Oak Board | See cable drawing | Wiring |  |  | Custom Order | 1
151 | Adhesive-Back Foam Sheet | 1/8" Thick | Other | McMaster | 8613K11 | McMaster | 1 | Per sheet. Cut to size.
152 | Ziptie | 92mmx2.3mm | Other | Thomas & Betts | TY23MX | Amazon | 1 | Pack of 1000
Screws
153 | Thread-Forming Screws T6 Torx Drive | M2 x 6 mm Long | Hardware | McMaster | 96817A312 | McMaster | 8 | Pack of 25, Drill bit: 30585A74 | $1.47
154 | Thread-Forming Screws T8 Torx Drive | M2.5 x 6 mm Long | Hardware | McMaster | 96817A317 | McMaster | 4 | Pack of 50, Drill bit: 30585A69 | $1.47
155 | Zinc-Plated Alloy Steel Hex Drive FHCS | M2 x 0.40 mm Thread Size, 4 mm Long | Hardware | McMaster | 91263A411 | McMaster | 8 | Pack of 50
156 | Zinc-Plated Steel T6 Torx FHCS | M2 x 0.4 mm Thread Size, 12 mm Long | Hardware | McMaster | 90236A107 | McMaster | 36 | Pack of 50
157 | Zinc-Plated Alloy Steel Hex Drive FHCS | M2.5 x 0.45 mm Thread Size, 5 mm Long | Hardware | McMaster | 91263A421 | McMaster | 4 | Pack of 50
158 | Zinc-Plated Alloy Steel Hex Drive FHCS | M3 x 0.5 mm Thread, 8 mm Long | Hardware | McMaster | 91263A823 | McMaster | 6 | Pack of 100
159 | Black-Oxide Alloy Steel Hex Drive FHCS | M3 x 0.50 mm Thread, 10 mm Long | Hardware | McMaster | 91294A130 | McMaster | 6 | Pack of 100
160 | Black-Oxide Alloy Steel Hex Drive FHCS | M3 x 0.50 mm Thread, 12 mm Long | Hardware | McMaster | 91294A132 | McMaster | 2
161 | Black-Oxide Alloy Steel Hex Drive FHCS | M3 x 0.50 mm Thread, 16 mm Long | Hardware | McMaster | 91294A134 | McMaster | 3 | Pack of 100
162 | Black-Oxide Alloy Steel Hex Drive FHCS | M3 x 0.50 mm Thread, 22 mm Long | Hardware | McMaster | 91294A137 | McMaster | 3 | Pack of 50
163 | Black-Oxide Alloy Steel Hex Drive FHCS | M5 x 0.80 mm Thread, 40 mm Long | Hardware | McMaster | 91294A219 | McMaster | 4 | Pack of 50
164 | Zinc-Plated Alloy Steel Hex Drive SHCS | M2 x 0.4 mm Thread, 5 mm Long | Hardware | McMaster | 90128A177 | McMaster | 8 | Pack of 100
165 | Zinc-Plated Alloy Steel Hex DriveSHCS | M2 x 0.4 mm Thread, 6 mm Long | Hardware | McMaster | 90128A178 | McMaster | 20 | Pack of 100
166 | Zinc-Plated Alloy Hex Drive Steel SHCS | M2 x 0.4 mm Thread, 8 mm Long | Hardware | McMaster | 90128A179 | McMaster | 15 | Pack of 100
167 | Zinc-Plated Alloy Hex Drive Steel SHCS | M4 x 0.7 mm Thread, 20 mm Long | Hardware | McMaster | 90128A216 | McMaster |  | Pack of 100
168 | Black Oxide Alloy Hex Drive Steel SHCS | M2.5 x 0.45 mm Thread, 5 mm Long | Hardware | McMaster | 91290A100 | McMaster | 16 | Pack of 50
169 | Black Oxide Alloy Hex Drive Steel SHCS | M2.5 x 0.45 mm Thread, 12 mm Long | Hardware | McMaster | 91290A104 | McMaster | 4 | Pack of 100
170 | Black Oxide Alloy Steel Hex Drive SHCS | M2.5 x 0.45 mm Thread, 16 mm Long | Hardware | McMaster | 91290A106 | McMaster | 6 | Pack of 50
171 | Black Oxide Alloy Steel Hex Drive SHCS | M2 x 0.4 mm Thread, 5 mm Long | Hardware | McMaster | 91290A012 | McMaster | 10 | Pack of 100
172 | Black Oxide Alloy Steel Hex Drive SHCS | M2 x 0.4 mm Thread, 16 mm Long | Hardware | McMaster | 91290A047 | McMaster | 3 | Pack of 100
173 | Black Oxide Alloy Steel Hex Drive SHCS | M3 x 0.5 mm Thread, 6 mm Long | Hardware | McMaster | 91290A111 | McMaster | 148 | 2x Pack of 100
174 | Black Oxide Alloy Hex Drive Steel SHCS | M3 x 0.5 mm Thread, 8 mm Long | Hardware | McMaster | 91290A113 | McMaster | 43 | Pack of 100
175 | Black Oxide Alloy Steel Hex Drive SHCS | M3 x 0.5 mm Thread, 10 mm Long | Hardware | McMaster | 91290A115 | McMaster | 76 | Pack of 100
176 | Black Oxide Alloy Steel Hex Drive SHCS | M3 x 0.5 mm Thread, 12 mm Long | Hardware | McMaster | 91290A117 | McMaster | 81 | Pack of 100
177 | Black Oxide Alloy Steel Hex Drive SHCS | M3 x 0.5 mm Thread, 20 mm Long | Hardware | McMaster | 91290A123 | McMaster | 19 | Pack of 100
178 | Black Oxide Alloy Steel Hex Drive SHCS | M4 x 0.7 mm Thread, 8 mm Long | Hardware | McMaster | 91290A140 | McMaster | 78 | Pack of 100
179 | Black Oxide Alloy Steel Hex Drive SHCS | M4 x 0.7 mm Thread, 16 mm Long | Hardware | McMaster | 91290A154 | McMaster | 8 | Pack of 100
180 | Black-Oxide 18-8 Stainless Steel Hex Drive BHCS | M4 x 0.70 mm Thread, 16 mm Long | Hardware | McMaster | 97763A425 | McMaster | 16 | 2x Pack of 10
181 | Black-Oxide Alloy Steel Hex Drive BHCS | M4 x 0.70 mm Thread, 20 mm Long | Hardware | McMaster | 91239A152 | McMaster | 6 | Pack of 100
182 | Nylon PH Phillips Screws | M2 x 0.40 mm Thread, 10mm Long | Hardware | McMaster | 92492A705 | McMaster | 36 | Pack of 100
183 | Nylon PH Phillips Screws | M3 x 0.50 mm Thread, 12mm | Hardware | McMaster | 92492A719 | McMaster | 36 | Pack of 100
184 | Nylon Plastic Hex Drive SHCS | M3 x 0.5 mm Thread, 6 mm Long | Hardware | McMaster | 93640A142 | McMaster | 12 | Pack of 100
185 | Blue-Dyed Zinc-Plated Alloy Steel Hex Drive SHCS | M3 x 0.5 mm Thread, 8 mm Long | Hardware | McMaster | 91502A103 | McMaster | 21 | Pack of 100
186 | Black-Oxide Alloy Steel Hex Drive FHCS | M4 x 0.70 mm Thread, 20 mm Long | Hardware | McMaster | 91294A196 | McMaster | 10 | Pack of 100
187 | 18-8 Stainless Steel Nylon-Insert Locknut | M2 x 0.4 mm Thread | Hardware | McMaster | 93625A101 | McMaster | 3 | Pack of 10
188 | Black-Oxide 18-8 Stainless Steel Nylon-Insert Locknut | M3 x 0.5 Thread | Hardware | McMaster | 93625A223 | McMaster | 12 | 2x Pack of 10
189 | Zinc-Plated Steel Washer | M2 Screw Size, 2.200 mm ID, 4.500 mm OD | Hardware | McMaster | 98688A110 | McMaster | 8 | Pack of 100
190 | Zinc-Plated Steel Square Nut | M4 x 0.7 mm Thread | Hardware | McMaster | 96887A118 | McMaster | 4 | Pack of 25
191 | 18-8 Stainless Steel Dowel Pin | 3 x 5mm | Hardware | McMaster | 91585A334 | McMaster | 36 | Pack of 50
192 | Brass Tapered Heat-Set Inserts | M3 x 0.5 mm Thread, 3.8 mm Long | Hardware | McMaster | 94180A331 | McMaster | 10 | Pack of 100
193 | Brass Tapered Heat-Set Inserts | M4 x 0.7 mm Thread , 4.7 mm Lonth | Hardware | McMaster | 94180A351 | McMaster | 14 | Pack of 100
194 | Threadlocker, Loctite® 243 |  | Hardware | McMaster | 91458A116 | McMaster | 1
195 | Threadlocker, Loctite® 245 |  | Hardware | McMaster | 91458A370 | McMaster | 1
196 | Threadlocker, Loctite® 262 |  | Hardware | McMaster | 91458A180 | McMaster | 1

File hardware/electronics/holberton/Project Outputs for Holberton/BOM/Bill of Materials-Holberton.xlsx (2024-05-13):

Comment | Description | Designator | Footprint | LibRef | Quantity
__Template_Cap | CAP, CER, X5R, 0.1uF, 10%, 50V, 0402, 0.55mm, CAP, CER, X5R, 10uF, 10V, 20%, 0402, 0.7mm T, CAP, CER, X5R, 1uF, 10%, 25V, 0402, CAP, CER, X7R, 0.01uF, 50V, 20%, 0402, 0.56mm T, CAP, CER, X7R, 0.015uF, 25V, 10%, 0402, 0.56mm T, CAP CER 0402 220NF 16VDC X7R, CAP, CER, X5R, 4.7uF, 20%, 6.3V, 0402, 0.65mm, CAP, CER, C0G, 47PF, 5%, 50V, 0402 | C1, C2, C3, C9, C14, C15, C16, C18, C19, C20, C21, C22, C23, C24, C45, C53, C54, C55, C56, C58, C64, C77, C79, C84, C86, C89, C94, C95, C99, C103, C109, C110, C113, C123, C127, C132, C134, C135, C136, C137, C138, C139, C140, C141, C142, C143, C144, C146, C147, C148, C149, C151, C152, C153, C154, C159, C160, C168, C169, C170, C171, C172, C173, C174 | C0402 | 1762, 215, 1717, 625, 838, 1238, 50, 1447 | 64
__Template_Cap | CAP, CER, NP0, 15pF, 25V, 5%, 0201, 0.9mm T, CAP, CER, X7R, 220pF, 16V, 10%, 0201, 0.33mm T, CAP, CER, X5R, 1uF, 6.3V, 20%, 0201, 0.33mm T, CAP, CER, X5R, 0.01uF, 16V, 10%, 0201, 0.33mm T, CAP, CER, X5R, 3300pF, 10V, 10%, 0201, 0.33mm T, CAP, CER, NP0, 3.3pF, 50V, +/-0.25pF, 0201, 0.33mm T, CAP, CER, X5R, 2.2uF, 6.3V, 20%, 0201, 0.39mm T, CAP, CER, X7R, 100pF, 25V, 10%, 0201, 0.33mm T | C4, C11, C27, C59, C66, C69, C82, C83, C87, C97, C107, C118, C121, C124, C125, C126, C128, C131 | C0201 | 1033, 156, 240, 361, 343, 589, 110, 767 | 18
__Template_Cap_Auto | CAP, CER, X6S, 0.1uF, 10V, 10%, 0201, AUTOGRADE | C5, C10, C29, C51, C52, C62, C63, C67, C68, C70, C71, C72, C73, C74, C75, C76, C78, C81, C88, C90, C91, C92, C93, C96, C98, C100, C101, C102, C104, C105, C106, C108, C111, C112, C114, C115, C116, C117, C119, C120, C122, C129, C155, C156, C157, C158, C163, C164, C165, C166, C167 | C0201 | 934 | 51
22uF | CAP CER 22UF 35V X5R 1206 | C6, C65 | C1206 | 163 | 2
__Template_Cap_Auto | CAP, CER, X7R, 47uF, 16V, 20%, AUTO GRADE, 2220, 2.5mm T | C7, C8 | C2220 | 163 | 2
__Template_Cap | CAP, CER, X7S, 15uF, 100V, 20%, 2220, 2.8mm T | C17, C46, C47, C48, C50 | C2220 | 207 | 5
__Template_Cap_Auto | CAP, CER, X7S, 1uF, 20%, 100V, 0805 | C25, C30, C150, C161, C162 | C0805 | 1093 | 5
__Template_Cap_Auto | CAP, CER, X7S, 0.1uF, 100V, 10%, 0603, AUTOGRADE | C26, C31_PHA, C31_PHB, C31_PHC, C145 | C0603 | 1039 | 5
__Template_Cap | CAP, CER, X7R, 0.047uF, 100V, 10%, 0603, AUTOGRADE | C28 | C0603 | 1838 | 1
2.2nF | Multilayer Ceramic Capacitors MLCC - SMD/SMT 0603 2.2nF 100volts X7R 10% | C35_PHA, C35_PHB, C35_PHC | C0603 | C | 3
4.7UF | CAP CER 4.7UF 100V X7S 1210 | C37_PHA, C37_PHB, C37_PHC | C1210 | CAP_CER_1210_4.7UF_100V_20%_X7S | 3
__Template_Cap | CAP CER 22UF 100V X7S SMD (6.00mm x 5.00mm x 5.5mm) | C40, C44, C49 | CAP_CKG57NX7S2A226M500JJ | 207 | 3
1nF | Multilayer Ceramic Capacitors MLCC - SMD/SMT 0603 1.0nF 100volts X7R 10% | C41_PHA, C41_PHB, C41_PHC | C0603 | C | 3
__Template_Cap_Auto | CAP, CER, X7S, 1000PF, 2KV, 10%, 1210 | C57, C80 | C1210 | 6 | 2
__Template_Cap | CAP, CER, X5R, 10uF, 50V, 20%, 1210 | C85 | C1210 | 1813 | 1
POWER | LED, GREEN, 569nm, 30mA, CLEAR, 0603 | D1 | LEDSC160X80X90L40-GREEN | 97055cde-46be-5a44-ad2e-f3c9fb2da68b | 1
STO | LED, BLUE, 470nm, 15mA, DIFFUSED, 0603 | D2 | LEDSC160X80X90L40-BLUE | f11939b8-268a-575b-b7c2-77af98891583 | 1
3.3V | TVS, DIODE, UNIDIR, 3.3VRWM, 4.8VBR, 7.8VCL, SOD-923 | D3, D4, D5, D6, D7, D8, D10, D14, D15, D16, D17, D18, D19, D20, D21, D22, D23, D24 | SOD1060X40 | 192 | 18
__Template_Diode_Schottky_A/K | DIODE, SCHOTTKY, 100V, 1A, POWERDI123 | D9 | POWERDI123_DFLS1100-7 | 203 | 1
__Template_Diode_TVS_A/K | DIODE, TVS, UNI-DIR, 70VR, 100VCL, 400W, 140PF @1MHZ, SMA | D11 | SMA_B130-13-F | 200 | 1
24V | DIODE, TVS, UNIDIR, DUAL, 24VRWM, 26VBR, 41VCL, SOT-23-3 | D12 | 3SOT23 | 176 | 1
__Template_DIODE_SCHOTTKY | DIODE, SCHOTTKY, 30V VRRM, 1A IO, 12A SURGE, SOD-123 | D13 | SOD-123_H1.35MM | 290 | 1
LAIRD MI0603L221R-10 | FERRITE BEAD 220 OHM 0603 1LN | FB1, FB4, FB5, FB6, FB7, FB8 | INDC160X80X105L30N | f5bd4cf1-070f-4480-bf1a-f8cba0e78574, LAIRD_MI0603L221R-10 | 6
__Template_Ferrite_Bead | FERRITE, BEAD, 600OHMS @100MHZ, 25%, 250mA, 900 mOHM DCR, 0201 | FB2 | L0201_H0.33MM | 867 | 1
FB_ARRAY_BLA31AG221SN4D | FERRITE, BEAD, 220 OHM, 150mA, DCR 0.25 MAX, 1206 | FB3 | FB_ARRAY_BLA31AG221SN4D | 937 | 1
SAMTEC_FLE-104-01-G-DV-TR | CONN RCPT .05" 8POS DUAL SMD | J1 | SAMTEC_FLE-104-01-G-DV-TR | SAMTEC_FLE-104-01-G-DV-TR | 1
MOLEX_2X4_NANOFIT_1053141308 | CONN HEADER R/A 8POS 2.5MM | J2, J4 | MOLEX_1053141308 | MOLEX_2X4_NANOFIT_1053141308 | 2
M55-7102042R | CONN HEADER SMD R/A 20POS 1.27MM | J3 | CON_M55-7102042R | 1204 | 1
DNP | CONN HEADER VERT 2POS 2.5MM | J5 | Molex 1053092302 | Molex 1053092302 | 1
4.7uH | FIXED IND 4.7UH 3.9A 44MOHM SMD | L1 | IND_78438357047 | BOURNS_SRR1050A-180Y | 1
__Template_Inductor | IND, WIREWOUND, SHIELDED, 2.2uH, 2.1A, 20%, DCR 0.11, SMD, AUTOGRADE | L2 | IND_LPS3015-152MRB | 939 | 1
__Template_Inductor | 220 µH Semi-Shielded Drum Core, Wirewound Inductor 500 mA 1.4Ohm Nonstandard | L3 | IND_74404054221 | 938 | 1
COILCRAFT_LPS3015-473 | COILCRAFT LPS3015-473MRB INDUCTOR, SHLD, 47UH, 20%, 0.3A, SMD | L4 | COILCRAFT_LPS3015-473 | COILCRAFT_LPS3015-473 | 1
__Template_LED_GREEN_AK | LED, GREEN, 574nm, 2mA, CLEAR, 0402 | LED1, LED2, LED3 | LED_APHHS1005LCGCK | 306 | 3
__Template_LED_RED_AK | LED, RED, 640NM, 2mA, CLEAR, 0402 | LED4 | LED_APHHS1005LCGCK | 309 | 1
__Template_LED_ORANGE_AK | LED, ORANGE, 611NM, 10mA, CLEAR, 0201 | LED5, LED6, LED8, LED9 | LED_APG0603SYC-TT | 308 | 4
__Template_LED_YELLOW_AK | LED, YELLOW, 591NM, 10mA, CLEAR, 0201 | LED7, LED10 | LED_APG0603SYC-TT | 307 | 2
APHHS1005SURCK | LED RED CLEAR CHIP SMD | LED11 | LED_APHHS1005SURCK | APHHS1005SURCK | 1
SML-P11DTT86R | LED ORANGE CLEAR 1006 SMD | LED12 | LED_SML-P11DTT86R | SML-P11DTT86R | 1
Keystone_8737 | Motor lead attachement points Keystone_8737 | M6, M7, M8 | Keystone_8737 | MtgHole_1 | 3
 | PCB | PCB1 |  | 110 | 1
PFET_RSF010P05TL | MOSFET, PWR, P-CH, 45VDS, 1A ID, 460mOhm@ 1A, SMD-3 | Q1, Q2 | TUMT3 | 171 | 2
ONSEMI BSS123 | XSTR, MOSFET, ENHANCEMENT MODE, N-CH, 100V, 0.17A, SOT23-3 | Q3, Q4 | SOT23-3P95_240X110L43N | ed20cc43-0059-5b34-85f4-540c7b2cf9db | 2
NFET_DMN3900UFA | MOSFET, N-CH, 30V, 0.55A, DMN3900 | Q5 | 3XDFN | 24 | 1
Bipolar NPN 3 Pins Transistor Gummel-Poon Model | TRANS NPN 40V 0.2A SOT23-3 | Q6 | SOT23-3 | BJT NPN_GP | 1
TI CSD19532Q5B | MOSFET N-CH 100V 100A 8SON | Q8_PHA, Q8_PHB, Q8_PHC, Q11_PHA, Q11_PHB, Q11_PHC | TI_SON5X6 | be020311-d2d7-4d79-a360-c856c6f37d83 | 6
0 | RES, 0, JUMPER, 1/16W, 0402 | R1, R4, R12, R22, R24, R25, R63, R64, R69, R86, R97, R98, R146, R163 | R0402 | 8004, 3, CMP-2002-08122-2 | 14
10K | RES, 10K, 1%, 1/10W, 0402, AUTOGRADE | R2, R18, R34, R37, R38, R44, R54, R55, R117, R118, R127, R128, R136, R139, R140, R141 | R0402 | 7216 | 16
31.2K | RES 31.2K OHM 1% 1/16W 0402 | R3 | R0402 | 4161 | 1
__Template_Resistor | RES, 10K, 1%, 1/20W, 0201, AUTOGRADE, RES, 22.1, 1%, 1/20W, 0201, AUTOGRADE, RES, 1K, 1%, 1/20W, 0201, AUTOGRADE, RES, 300, 1%, 1/20W, 0201, AUTOGRADE, RES, 4.7K, 1%, 1/20W, 0201, AUTOGRADE, RES, 68, 1%, 1/20W, 0201, AUTOGRADE | R5, R6, R7, R9, R10, R11, R20, R27, R29, R30, R31, R32, R35, R40, R48, R49, R50, R52, R53, R56, R62, R66, R67, R68, R70, R71, R72, R73, R77, R80, R81, R82, R83, R85, R87, R88, R89, R91, R92, R93, R94, R95, R96, R99, R100, R102, R103, R105, R106, R108, R109, R110, R111, R119, R122, R123, R124, R147, R148, R149, R150, R153, R154, R155, R156 | R0201 | 6783, 10012, 10010, 10025, 10014 | 65
1.3 | RES, 1.3, 1%, 1/2W, AUTOGRADE, 0805 | R8 | R0805 | 8516 | 1
133K | RES, 133K, 1%, 1/16W, 0402, AUTOGRADE | R13 | R0402 | 5074 | 1
100 | RES, 100, 1%, 1/10W, 0402, AUTO GRADE | R14, R15, R19, R112, R116, R144, R145, R151, R152, R158, R159 | R0402 | 7286 | 11
432K | RES, 432K, 1%, 1/16W, 0402 | R16, R28, R41, R43, R47, R135 | R0402 | 8801, 5492 | 6
1.15K | RES, 1.15K, 1%, 1/16W, 0402 | R17 | R0402 | 8684 | 1
__Template_Thermistor | SENSOR, THERMISTOR, NTC, 10K, 1%, 3380K, 100mW, 0402 | R21, RT1, RT2, RT3 | R0402 | 175 | 4
3.9R | RES SMD 3.9 OHM 5% 1/2W 0805 | R23_PHA, R23_PHB, R23_PHC | R0805 | R | 3
2.2R | RES SMD 2.2 OHM 1% 1/2W 0805 | R26_PHA, R26_PHB, R26_PHC | R0805 | R | 3
PANASONIC ERJ2RKF8202X | Res, 82k, +/-1%, 0.1W, 0402, AUTO GRADE | R33 | R0402 | 07680e2d-088d-5a06-a7a1-fe9cd6488fb2 | 1
PANASONIC ERJ2RKF1822X | Res, 18.2k, +/-1%, 0.1W, 0402, AUTO GRADE | R36 | R0402 | 78eec7e5-34dd-5b0c-8bd5-fdbc658ba047 | 1
6.19K | RES, 6.19K, 1%, 1/16W, 0402 | R39 | R0402 | 9146 | 1
56K | RES, 56K, 1%, 1/16W, 0402 | R42 | R0402 | 8099 | 1
75 | RES, 75, 1%, 1/16W, 0402 | R45, R61, R74, R84 | R0402 | 2283 | 4
68.1K | RES, 68.1K, 1%, 1/16W, 0402 | R46, R51, R79 | R0402 | 4849, 10007 | 3
8.2K | RES 8.2K OHM 1% 1/4W 1206 | R57, R58 | R1206 | 3733 | 2
2.2K | Resistor, 2.20K Ohms, 0201, 0.05W, ±1% | R59, R60 | R0201 | 3569 | 2
1 | RES, 1.0, 5%, 1/20W, 0201 | R65 | R0201 | 7413 | 1
10.2K | Resistor, 10.2K Ohms, 0201, 0.05W, ±1% | R75 | R0201 | 4161 | 1
1.96K | RES, 1.96K, 1%, 1/20W, 0201 | R76 | R0201 | 6790 | 1
86.6K | Resistor, 86.6K Ohms, 0201, 0.05W, ±1% | R78 | R0201 | 4926 | 1
200 | RES, 200, 1%, 1/20W, 0201, AUTOGRADE | R101, R104 | R0201 | 10010 | 2
100K | RES, 100K, 1%, 1/10W, 0603, AUTO GRADE | R114, R115, R120, R121, R125, R126, R129, R130, R131, R132, R133, R134, R137, R138, R142, R143 | R0603 | 6516 | 16
0.0015 OHM | RES, 0.0015, 1%, 3W, 2512 | R157, R160, R161, R162 | R2512 | 9999 | 4
KSR253GLFG | SWITCH TACTILE SPST-NO 0.01A 32V | SW1, SW2, SW3 | SW_KSR253GLFG | SW_2P-KSR253GLFG | 3
PULSE_H1102NL | Telecom Transformer 2(1:1) 0.65Ohm Prim. DCR 0.65Ohm Sec. DCR 16 Terminal Gull Wing SMD | T1, T2 | PULSE_HXXXX | PULSE_H1102NL | 2
TP_KEYSTONE_5015 | PC TEST POINT MINIATURE SMT | TP1, TP2 | TP_KEYSTONE_5015 | 176 | 2
TEST_KEYSTONE5001 | PC TEST POINT TH RING | TP3, TP12 | TP_KEYSTONE_5001 | TEST_KEYSTONE5001 | 2
TEST_KEYSTONE5015 | PC TEST POINT MINIATURE SMT | TP4, TP5, TP6, TP7, TP8, TP9, TP10, TP11 | TP_KEYSTONE_5015 | TEST_KEYSTONE5015 | 8
OPTO_HCPL-817-56CE | ISOLATOR, OPTOISOLATOR, PHOTO TRANSISTOR, 70V, 50mA, SMD-4 | U1, U2 | OPTO_HCPL-817-56CE | 276 | 2
EEPROM_M24256-DRMF3TG/K | IC, MEMORY, M24256, EEPROM, 256Kb, I2C, 1MHz, MLP-8, AUTOGRADE | U3 | 8WFDFN300X200X80-8-TP | 423 | 1
TPS62933PDRLR | IC REG BUCK ADJUSTABLE 3A SOT583 | U4 | SOT-583 | TI_TPS62933PDRLR | 1
PROCESSOR_TRINAMIC_TMC8462-BA | IC, CONTROLLER, TMC8462, ETHERNET, 100Mb, SPI, PWM O/P, 100mA, BGA-121 | U5 | BGA121C75P11X11_900X900X145 | 113 | 1
MCU_STM32H755IIK3 | IC, MCU, STM32H755xI, ARM, 32-BIT, 240MHZ, 128 I/O, 2MB, FLASH, 1.62V TO 3.6V, UFBGA-201 | U6 | BGS201C65P15X15_1000X1000X60 | 112 | 1
SENSOR_ST_LSM6DSOTR | Accelerometer, Gyroscope, 6 Axis Sensor I²C, SPI Output | U8 | 14-LGA | LSM6DSOTR | 1
SENSOR_ST_IIS2MDCTR | SENSOR MR I2C/SPI 12LGA | U9 | 12-LGA | IIS2MDCTR | 1
MCP6064 | Microchip MCP6064-E/ST; Quad Op Amp; 0.73MHz CMOS; Rail to Rail; 3V; 5V; 14-Pin TSSOP | U10, U14, U17 | 14TSSOP65 | MICROCHIP_MCP6064 | 3
MOTOR_DRIVE_DRV8353RSRGZT | IC, MOTOR DRIVER, DRV8353, MULTIPHASE, BLDC, HALF BRIDGE, POWER MOSFET, 6V TO 95V VIN, VQFN-48 | U11 | VQFN50P700X700X100-48-TP_TP-CUST_NO_VIAS | 820 | 1
INA240A1DR | Current Sense Amplifiers -4 to 80V, bidirectional, ultra-precise current sense amplifier with enhanced PWM rejection, 20V/V gain | U12, U13, U16, U20 | TI SOIC-8 D0008A | INA240A1 | 4
TPS72733DSET | IC REG LINEAR 3.3V 250MA 6WSON | U15 | 6WSON | CMP-0394-01493-2 | 1
TI_TPS54331GDR | Conv DC-DC Single Step Down 3.5V to 28V 8-Pin SOIC T/R | U18 | SOIC127P600X175-8N | TI_TPS54331GDR | 1
MPS_MA732GQ-Z | 14-BIT, DIGITAL, CONTACTLESS ANG | U19 | MPS_MA732GQ-Z | MPS_MA732GQ-Z | 1
XTAL_SIT8924BM-72-33N-100.000000 | OSC, MEMS, XO, 100MHZ, +/-25PPM STAB, LVCMOS, 3.3V, SMD-4, AUTOGRADE | X1 | XTAL_SIT8924BM-72-33N-100.000000 | 137 | 1

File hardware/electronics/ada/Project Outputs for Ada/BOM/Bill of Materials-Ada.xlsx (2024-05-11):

Comment | Description | Designator | Footprint | LibRef | Quantity
CL03A105MQ3CSNC | Cap Ceramic 1uF 6.3V X5R ±20% Pad SMD 0201 +85°C T/R | C1, C2, C3, C6 | FP-CL03-IPC_A | CMP-13271-003873-1 | 4
C0402C103M5RACTU | CAP CER 10000PF 50V 20% X7R 0402 | C4 | FP-C0402-BB-MFG | CMP-1034-01887-3 | 1
CC0402KRX5R9BB104 | CAP CER 0.1UF 50V X5R 0402 | C5, C7 | FP-CC0402-MFG | CMP-03422-000742-1 | 2
RCLAMP1521PQTCT | TVS Diode (Bi-directional) | D1 | RCLAMP1521PQTCT | RCLAMP1521PQTCT | 1
SML-P11DTT86R | LED ORANGE CLEAR 1006 SMD | D2 | FP-SML-P11-MFG | CMP-08952-000022-1 | 1
APHHS1005SURCK | LED RED CLEAR CHIP SMD | D3 | FP-APHHS1005SURCK-MFG | CMP-2000-05787-2 | 1
QBLP595-IB | LED BLUE CLEAR 0402 SMD | D4 | FP-QBLP595-IB-MFG | CMP-113271-000002-1 | 1
10114830-11108LF | Connector | J1 | 1011483011108LF | 10114830-11108LF | 1
1053092302 | Connector | J2 | 105309YY02_U | 1053092302 | 1
PCB | PCB | PCB1 |  | 110 | 1
432K |  | R1 | RESC1005X40X25NL05T10 | CMP-2002-07684-1 | 1
ERJ-2RKF2000X | RES SMD 200 OHM 1% 1/10W 0402 | R2, R3, R4 | FP-ERJ2RK-IPC_A | CMP-2002-00757-2 | 3
NCP15XH103F03RC | Thermistor | RT1 | THRMC1005X55N | NCP15XH103F03RC | 1
SENSOR_MPS_MA732 | SENSOR, ANGLE, 9 BIT TO 14 BIT RESOLUTION, 14-BIT PWM OUTPUT, 3.3V, 12mA, QFN-16 | U1 | QFN50P300X300X100-16-TP | 165 | 1
ADP150AUJZ-3.3-R7 | Ultralow Noise, 150 mA CMOS Linear Regulator, 2.2 to 5.5 V Vin, 3.3 V Vout, Industrial, 5-pin SOT23 (UJ-5), Reel | U2 | ADI-UJ-5_M | CMP-0786-00394-1 | 1

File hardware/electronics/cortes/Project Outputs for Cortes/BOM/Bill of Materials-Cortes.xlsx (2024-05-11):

Comment | Description | Designator | Footprint | LibRef | Quantity
__Template_Cap | CAP, CER, X7R, 0.01uF, 50V, 20%, 0402, 0.56mm T, CAP, CER, X5R, 10uF, 10V, 20%, 0402, 0.7mm T, CAP, CER, X5R, 0.1uF, 10%, 50V, 0402, 0.55mm, CAP, CER, X7R, 0.015uF, 25V, 10%, 0402, 0.56mm T, CAP, CER, X5R, 4.7uF, 20%, 6.3V, 0402, 0.65mm, CAP, CER, X7R, 3900pF, 50V, 10%, 0402, 0.56mm T | C1, C4, C27, C30, C43, C45, C51, C52, C60, C61, C62, C63, C76, C81, C87, C91, C92, C97, C98, C100, C102, C103 | C0402 | 625, 215, 1762, 838, 50, 377 | 22
__Template_Cap_Auto | CAP, CER, X6S, 0.1uF, 10V, 10%, 0201, AUTOGRADE | C2, C3, C6, C7, C9, C11, C13, C14, C15, C16, C17, C18, C19, C20, C21, C22, C23, C24, C25, C28, C29, C33, C34, C35, C36, C37, C38, C39, C40, C41, C42, C48, C54, C58, C59, C66, C67, C68, C69, C70, C71, C72, C73, C74, C75, C80, C84, C85, C86, C89, C94 | C0201Y | 934 | 51
__Template_Cap | CAP, CER, X5R, 0.01uF, 16V, 10%, 0201, 0.33mm T, CAP, CER, X7R, 220pF, 16V, 10%, 0201, 0.33mm T, CAP, CER, X7R, 100pF, 25V, 10%, 0201, 0.33mm T, CAP, CER, X7R, 0.01uF, 10V, 10%, AUTO GRADE, 0201, 0.33mm T, CAP, CER, NP0, 3.3pF, 50V, +/-0.25pF, 0201, 0.33mm T, CAP, CER, NP0, 10pf, 50V, 5%, 0201, 0.33mm T | C5, C8, C10, C12, C31, C32, C49, C53, C77, C78, C83, C93, C95, C99 | C0201Y | 1238, 156, 767, 361, 589, 49 | 14
__Template_Cap | CAP, CER, NP0, 15pF, 25V, 5%, 0201, 0.9mm T, CAP, CER, X5R, 1uF, 6.3V, 20%, 0201, 0.33mm T, CAP, CER, X5R, 2.2uF, 6.3V, 20%, 0201, 0.39mm T, CAP, CER, X5R, 3300pF, 10V, 10%, 0201, 0.33mm T | C26, C50, C79, C82, C88, C90, C96 | C0201 | 1033, 240, 110, 343 | 7
__Template_Cap | CAP, CER, X5R, 10uF, 50V, 20%, 1210 | C44, C101 | C1210_H2.7mm | 1813 | 2
__Template_Cap_Auto | CAP, CER, X7R, 47uF, 16V, 20%, AUTO GRADE, 2220, 2.5mm T | C46, C47, C55, C56, C57 | C2220 | 163 | 5
__Template_Cap_Auto | CAP, CER, X7S, 1000PF, 2KV, 10%, 1210 | C64, C65 | C1210 | 6 | 2
3.3 | TVS, DIODE, UNIDIR, 3.3VRWM, 4.8VBR, 7.8VCL, SOD-923 | D1, D2, D3, D4, D5, D6, D7, D8, D9, D10, D11, D12, D13, D14, D15, D16, D17, D18, D19, D20, D21, D22 | SOD1060X40 | 192 | 22
24V | DIODE, TVS, UNIDIR, DUAL, 24VRWM, 26VBR, 41VCL, SOT-23-3 | D23 | 3SOT23 | 176 | 1
__Template_DIODE_SCHOTTKY | DIODE, SCHOTTKY, 30V VRRM, 1A IO, 12A SURGE, SOD-123 | D24 | SOD-123_H1.35MM | 290 | 1
__Template_Diode_Schottky_A/K | DIODE, SCHOTTKY, 60V, 3A, DO220AA | D25 | DO-220AA_A/K | 35 | 1
__Template_Ferrite_Bead | FERRITE, BEAD, 600OHMS @100MHZ, 25%, 250mA, 900 mOHM DCR, 0201 | FB1 | L0201_H0.33MM | 867 | 1
LAIRD MI0603L221R-10 | LAIRD - MI0603L221R-10 - Ferrite Bead, 0603 [1608 Metric], 220 ohm, 2 A, MI Series, 0.05 ohm | FB2, FB3 | INDC160X80X105L30N | LAIRD_MI0603L221R-10 | 2
FB_ARRAY_BLA31AG221SN4D | FERRITE, BEAD, 220 OHM, 150mA, DCR 0.25 MAX, 1206 | FB4 | FB_ARRAY_BLA31AG221SN4D | 937 | 1
 | CONN, HDR, SHRD, RA, 2x10, 1.27MM P, 6.02MM h, GOLD, TH | J1 | SAMTEC_TFM-110-02-L-DH | 1204 | 1
 | CONN, RCPT, FEMALE, 30 P, 1.27MM, 2.45MM H, GOLD, SMD | J2, J3 | HARWIN_M50-3151542 | 1205 | 2
MOLEX_2X5_NANOFIT_1053141210 | Conn HDR 10 POS 2.5mm Solder RA Thru-Hole 10 Terminal 1 Port | J4, J5 | MOLEX_1053141210 | MOLEX_2X5_NANOFIT_1053141210 | 2
SAMTEC_FLE-104-01-G-DV-TR | CONN RCPT .05" 8POS DUAL SMD | J6 | SAMTEC_FLE-104-01-G-DV-TR | SAMTEC_FLE-104-01-G-DV-TR | 1
__Template_Inductor | IND, WIREWOUND, SHIELDED, 2.2uH, 2.1A, 20%, DCR 0.11, SMD, AUTOGRADE | L1 | IND_LPS3015-152MRB | 939 | 1
COILCRAFT_LPS3015-473 | COILCRAFT LPS3015-473MRB INDUCTOR, SHLD, 47UH, 20%, 0.3A, SMD | L2 | IND_LPS3015-152MRB | COILCRAFT_LPS3015-473 | 1
BOURNS_SRR1050A-180Y | FIXED IND 18UH 3.1A 51 MOHM SMD | L3 | INDP100100X51N | BOURNS_SRR1050A-180Y | 1
__Template_LED_YELLOW_AK | LED, YELLOW, 591NM, 10mA, CLEAR, 0201 | LED1, LED7 | LED_APG0603SYC-TT | 307 | 2
__Template_LED_ORANGE_AK | LED, ORANGE, 611NM, 10mA, CLEAR, 0201 | LED2, LED8, LED9 | LED_APG0603SYC-TT | 308 | 3
__Template_LED_GREEN_AK | LED, GREEN, 574nm, 2mA, CLEAR, 0402 | LED3, LED4, LED5 | LED_APHHS1005LCGCK | 306 | 3
__Template_LED_RED_AK | LED, RED, 640NM, 2mA, CLEAR, 0402 | LED6 | LED_APHHS1005LCGCK | 309 | 1
3.7mm hole 5mm pad | 3.7mm hole 5mm pad | M1, M2, M3 | 3.7hole5pad | MtgHole | 3
SPH0641LM4H-1 | MORELLO MIC MULTIMODE DGT BOT PT | MIC1, MIC2 | FP-SPH0641LM4H-1-MFG | CMP-95043-000005-1 | 2
PCB | PCB | PCB1 |  | 110 | 1
NFET_DMN3900UFA | MOSFET, N-CH, 30V, 0.55A, DMN3900 | Q1 | 3XDFN | 24 | 1
 | Resistor, 432K Ohms, 0805, 0.125W, ±1% | R1, R81, R82 | R0805 | 5492 | 3
__Template_Resistor | RES, 10K, 1%, 1/20W, 0201, AUTOGRADE, RES, 49.9, 1%, 1/20W, 0201, AUTOGRADE, RES, 22.1, 1%, 1/20W, 0201, AUTOGRADE, RES, 68, 1%, 1/20W, 0201, AUTOGRADE, RES, 1K, 1%, 1/20W, 0201, AUTOGRADE, RES, 4.7K, 1%, 1/20W, 0201, AUTOGRADE, RES, 68.1K, 1%, 1/20W, 0201, AUTOGRADE | R2, R3, R4, R5, R6, R7, R8, R9, R10, R11, R12, R13, R14, R15, R16, R17, R18, R19, R20, R21, R22, R23, R24, R25, R26, R27, R28, R29, R30, R31, R33, R35, R36, R37, R38, R39, R40, R41, R42, R43, R44, R45, R46, R47, R48, R49, R51, R52, R53, R54, R55, R56, R59, R60, R61, R64, R65, R66, R67, R68, R69, R70, R75, R76 | R0201_H0.26MM | 6783, 10006, 10012, 10014, 10010, 10025, 10007 | 64
__Template_Resistor | RES, JUMPER, 0, 1/10W, 0603 | R32, R34 | R0603 | 3 | 2
 | RES, 1.0, 5%, 1/20W, 0201, Resistor, 10.2K Ohms, 0201, 0.05W, ±1%, RES, 1.96K, 1%, 1/20W, 0201, Resistor, 86.6K Ohms, 0201, 0.05W, ±1%, Resistor, 13.3K Ohms, 0201, 0.05W, ±1%, RES, 3.24K, 1%, 1/20W, 0201, Resistor, 2.20K Ohms, 0201, 0.05W, ±1% | R50, R57, R58, R62, R63, R77, R78, R83, R84 | R0201 | 7413, 4161, 6790, 4926, 4248, 7433, 3569 | 9
 | RES, 75, 1%, 1/16W, 0402, RES, 0, JUMPER, 1/16W, 0402 | R71, R72, R73, R74, R79, R80, R85, R86, R87 | R0402 | 2283, 8004 | 9
DNP | RES Thick Film, 0Ω, 0.063W, 0402 | R88 | FP-CRCW0402-e3-IPC_C | CMP-2002-08122-2 | 1
PULSE_H1102NL | Telecom Transformer 2(1:1) 0.65Ohm Prim. DCR 0.65Ohm Sec. DCR 16 Terminal Gull Wing SMD | T1, T2 | PULSE_HXXXX | PULSE_H1102NL | 2
TEST_KEYSTONE5001 | PC TEST POINT TH RING | TP1, TP2 | TP_KEYSTONE_5001 | TEST_KEYSTONE5001 | 2
KEYSTONE5015_NOSILK | HW, TEST POINT, NO SILKSCREEN, PC MINIATURE, 0.25mm T, 1.52mm HEIGHT, SILVER PLATING, SMT | TP3, TP4 | KEYSTONE_5015_NS | 176 | 2
SENSOR_ST_LSM9DS1TR | SENSOR, MOTION, IMU, ACCELEROMETER/GYROSCOPE/MAGNETOMETER, I2C, SPI, LGA-24 | U1 | LGA24RX8X4_350X100X102 | 172 | 1
MCU_STM32H755IIK3 | IC, MCU, STM32H755xI, ARM, 32-BIT, 240MHZ, 128 I/O, 2MB, FLASH, 1.62V TO 3.6V, UFBGA-201 | U2 | BGS201C65P15X15_1000X1000X60 | 112 | 1
MCP6064 | Microchip MCP6064-E/ST; Quad Op Amp; 0.73MHz CMOS; Rail to Rail; 3V; 5V; 14-Pin TSSOP | U3, U4 | 14TSSOP65 | MICROCHIP_MCP6064 | 2
PROCESSOR_TRINAMIC_TMC8462-BA | IC, CONTROLLER, TMC8462, ETHERNET, 100Mb, SPI, PWM O/P, 100mA, BGA-121 | U5 | BGA121C75P11X11_900X900X145 | 113 | 1
EEPROM_M24256-DRMF3TG/K | IC, MEMORY, M24256, EEPROM, 256Kb, I2C, 1MHz, MLP-8, AUTOGRADE | U6 | 8WFDFN300X200X80-8-TP | 423 | 1
TI_TPS54331GDR | Conv DC-DC Single Step Down 3.5V to 28V 8-Pin SOIC T/R | U7, U9 | SOIC127P600X175-8N | TI_TPS54331GDR | 2
TPS72733DSET | Single Output Fast Transient Response LDO, 250 mA, Fixed 3.3 V Output, 2 to 5.5 V Input, with Ultra-Low IQ, 6-pin WSON (DSE), -40 to 125 degC, Green (RoHS & no Sb/Br) | U8 | DES0006A_V | CMP-0394-01493-2 | 1
XTAL_SIT8924BM-72-33N-100.000000 | OSC, MEMS, XO, 100MHZ, +/-25PPM STAB, LVCMOS, 3.3V, SMD-4, AUTOGRADE | X1 | XTAL_SIT8924BM-72-33N-100.000000 | 137 | 1

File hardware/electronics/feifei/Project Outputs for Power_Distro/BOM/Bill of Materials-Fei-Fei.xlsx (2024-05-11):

Comment | Description | Designator | Footprint | LibRef | Quantity
SMBJ58CA | Diode TVS Single Bi-Dir 58V 600W 2-Pin SMB | D1 | DO-214AA | SMBJ48A-13-F | 1
0154007.DRT | FUSE BRD MNT 7A 72VAC 60VDC 2SMD | F1, F2, F3, F4 | FP-0154-MFG | CMP-08605-000019-1 | 4
XT60PW-F |  | J1, J2, J3, J4 | XT60PW_F | XT60PW-F | 4
XT60E-M |  | J5 | XT60E-M | XT60E-M | 1
XT30U-F |  | J6, J7 | XT30U-F | XT30U-F | 2

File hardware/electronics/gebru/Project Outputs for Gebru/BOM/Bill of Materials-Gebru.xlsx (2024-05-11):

Comment | Description | Designator | Footprint | LibRef | Quantity
1nF | Automotive grade SMD 0603 capacitor such as Vishay GA....31G series. 1nF 0603 10% X7R 100V | C1A, C1B, C1C | CAP 0603_1608 RF | C | 3
2.2nF | Automotive grade SMD 0603 capacitor such as Vishay GA....31G series. 2.2nF 0603 10% X7R 100V | C2A, C2B, C2C | CAP 0603_1608 RF | C | 3
__Template_Cap_Auto | CAP, CER, X7S, 1uF, 20%, 100V, 0805 | C3, C4, C17, C18, C35 | C0805 | 1093 | 5
__Template_Cap | CAP, CER, X7R, 0.01uF, 50V, 20%, 0402, 0.56mm T, CAP, CER, X5R, 0.1uF, 10%, 50V, 0402, 0.55mm, CAP, CER, X5R, 1uF, 10%, 25V, 0402, CAP, CER, C0G, 47PF, 5%, 50V, 0402 | C5, C14, C21, C23, C24, C25, C26, C27, C28, C29, C30, C33, C37, C38, C39, C40, C41, C42, C43, C44, C45, C46, C47, C48, C49, C50, C51, C52, C53, C54, C55, C56, C57, C58, C59, C60, C61, C65, C66, C67, C68, C69, C70, C71, C72, C73 | C0402 | 625, 1762, 1717, 1447 | 46
WURTH 870056175004 | WCAP-PTHR ALUMINUM POLYMER CAP | C10, C11 | WURTH_WCAP-PTHR_10x12.5x5 | 31291c97-b9eb-436f-b2ee-2be21f893d37 | 2
__Template_Cap | CAP, CER, X7S, 15uF, 100V, 20%, 2220, 2.8mm T | C12, C13, C15, C19, C20, C34 | C2220 | 207 | 6
__Template_Cap_Auto | CAP, CER, X7S, 0.1uF, 100V, 10%, 0603, AUTOGRADE | C16, C36, C63A, C63B, C63C | C0603 | 1039 | 5
__Template_Cap | CAP, CER, X7R, 0.047uF, 100V, 10%, 0603, AUTOGRADE | C22 | C0603Y | 1838 | 1
__Template_Cap | CAP, CER, X5R, 10uF, 50V, 20%, 1210 | C31, C32 | C1210_H2.7mm | 1813 | 2
CAP_CER_1210_4.7UF_100V_20%_X7S | CAP CER 4.7UF 100V X7S 1210 | C62A, C62B, C62C | C1210 | CAP_CER_1210_4.7UF_100V_20%_X7S | 3
__Template_Diode_TVS_A/K | DIODE, TVS, UNI-DIR, 70VR, 100VCL, 400W, 140PF @1MHZ, SMA | D1 | SMA_B130-13-F | 200 | 1
POWER | LED, GREEN, 569nm, 30mA, CLEAR, 0603 | D2 | LEDSC160X80X90L40-GREEN | 97055cde-46be-5a44-ad2e-f3c9fb2da68b | 1
STO | LED, BLUE, 470nm, 15mA, DIFFUSED, 0603 | D3 | LEDSC160X80X90L40-BLUE | f11939b8-268a-575b-b7c2-77af98891583 | 1
__Template_Diode_Schottky_A/K | DIODE, SCHOTTKY, 100V, 1A, POWERDI123 | D10 | POWERDI123_DFLS1100-7 | 203 | 1
LAIRD MI0603L221R-10 | FERRITE BEAD 220 OHM 0603 1LN | FB2, FB3, FB4, FB5, FB6 | INDC160X80X105L30N | f5bd4cf1-070f-4480-bf1a-f8cba0e78574 | 5
 | CONN, FFC, RA, 1x6 P, 0.5MM PITCH, 2.3MM H, GOLD, SMD | J1 | MOLEX_FPC_527460671 | 1210 | 1
 | CONN, HDR, UNSHRD, VERT, 2x15 P, 1.27MM PITCH, 5.33MM H, GOLD, SMD | J4, J5 | HARWIN_M50-3601542 | 1207 | 2
__Template_Inductor | IND, WIREWOUND, SHIELDED, 220uH, 0.74A, 20%, DCR 0.624, SMD, AUTOGRADE | L10 | IND_MSS7348 | 938 | 1
3.7mm hole 5mm pad | 3.7mm hole 5mm pad | M8 | 3.7hole5pad | MtgHole | 1
9774040960R | Spacer Material: Steel Mounting: SMT Series: WA-SMST For ø: 3.3 mm | MTH5, MTH6, MTH7 | 9774040960R | Wurth_4mm_Spacer_9774040960R | 3
 | PCB | PCB1 |  | 110 | 1
TI CSD19532Q5B | MOSFET N-CH 100V 100A 8SON | Q1A, Q1B, Q1C, Q2A, Q2B, Q2C | TI_SON5X6 | be020311-d2d7-4d79-a360-c856c6f37d83 | 6
PFET_RSF010P05TL | MOSFET, PWR, P-CH, 45VDS, 1A ID, 460mOhm@ 1A, SMD-3 | Q3, Q4 | TUMT3 | 171 | 2
ONSEMI BSS123 | XSTR, MOSFET, ENHANCEMENT MODE, N-CH, 100V, 0.17A, SOT23-3 | Q5, Q6 | SOT23-3P95_240X110L43N | ed20cc43-0059-5b34-85f4-540c7b2cf9db | 2
 | Resistor, 3.30K Ohms, 1206, 0.25W, ±1% | R1, R4 | R1206 | 3733 | 2
PANASONIC ERJ2RKF1822X | Res, 18.2k, +/-1%, 0.1W, 0402, AUTO GRADE | R2 | RESC100X50X40L25 | 78eec7e5-34dd-5b0c-8bd5-fdbc658ba047 | 1
 | Resistor, 432K Ohms, 0805, 0.125W, ±1%, RES, 1.3, 1%, 1/2W, AUTOGRADE, 0805 | R3, R17, R56, R71, R72 | R0805 | 5492, 8516 | 5
 | RES, 100, 1%, 1/10W, 0402, AUTO GRADE | R5 | RES 0402_1005 RF | 7286 | 1
 | RES, 0.0015, 1%, 3W, 2512 | R6, R7, R8, R10 | R2512_H0.8MM | 9999 | 4
 | RES, 100, 1%, 1/10W, 0402, AUTO GRADE, RES, 0, JUMPER, 1/16W, 0402, RES, 432K, 1%, 1/16W, 0402, RES, 133K, 1%, 1/16W, 0402, AUTOGRADE, RES, 10K, 1%, 1/10W, 0402, AUTOGRADE, RES, 1.15K, 1%, 1/16W, 0402, RES, 56K, 1%, 1/16W, 0402, RES, 6.19K, 1%, 1/16W, 0402, RES, 68.1K, 1%, 1/16W, 0402 | R9, R11, R13, R14, R15, R16, R18, R19, R20, R22, R25, R26, R29, R32, R33, R36, R38, R40, R43, R46, R47, R50, R53, R57, R58, R59, R60, R61, R62, R63, R64, R65, R66, R69, R70 | R0402 | 7286, 8004, 8801, 5074, 7216, 8684, 8099, 9146, 4849 | 35
PANASONIC ERJ2RKF8202X | Res, 82k, +/-1%, 0.1W, 0402, AUTO GRADE | R21 | RESC100X50X40L25 | 07680e2d-088d-5a06-a7a1-fe9cd6488fb2 | 1
__Template_Thermistor | SENSOR, THERMISTOR, NTC, 10K, 1%, 3380K, 100mW, 0402 | R23 | R0402_H0.55MM | 175 | 1
3.9R | High power thick film 0805 resistor such as Vishay CRCW-HP e3 series CRCW08053R90DKEAHP | R24A, R24B, R24C | RES 0805_2012 RF | R | 3
 | RES, 100K, 1%, 1/10W, 0603, AUTO GRADE | R27, R28, R30, R31, R34, R35, R37, R39, R41, R42, R44, R45, R48, R49, R51, R52 | R0603 | 6516 | 16
2R | High power thick film 0805 resistor such as Vishay CRCW-HP e3 series CRCW08052R00DKEAHP | R54A, R54B, R54C | RES 0805_2012 RF | R | 3
TEST_KEYSTONE5001 | PC TEST POINT TH RING | TP1, TP2 | TP_KEYSTONE_5001 | TEST_KEYSTONE5001 | 2
TEST_KEYSTONE5015 | PC TEST POINT MINIATURE SMT | TP3, TP4, TP5, TP6, TP7, TP8, TP9, TP10 | TP_KEYSTONE_5015 | TEST_KEYSTONE5015 | 8
INA240A1D | Current Sense Amplifiers -4 to 80V, bidirectional, ultra-precise current sense amplifier with enhanced PWM rejection, 20V/V gain | U1, U2, U3, U10 | TI SOIC-8 D0008A | INA240A1 | 4
MCP6064 | Microchip MCP6064-E/ST; Quad Op Amp; 0.73MHz CMOS; Rail to Rail; 3V; 5V; 14-Pin TSSOP | U4 | 14TSSOP65 | MICROCHIP_MCP6064 | 1
OPTO_HCPL-817-56CE | ISOLATOR, OPTOISOLATOR, PHOTO TRANSISTOR, 70V, 50mA, SMD-4 | U5, U6 | OPTO_HCPL-817-56CE | 276 | 2
MOTOR_DRIVE_DRV8353RSRGZT | IC, MOTOR DRIVER, DRV8353, MULTIPHASE, BLDC, HALF BRIDGE, POWER MOSFET, 6V TO 95V VIN, VQFN-48 | U11 | VQFN50P700X700X100-48-TP_TP-CUST_NO_VIAS | 820 | 1

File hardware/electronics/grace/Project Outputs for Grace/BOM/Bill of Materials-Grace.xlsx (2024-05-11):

Comment | Description | Designator | Footprint | LibRef | Quantity
220uF | Polarised Capacitor | C1, C2, C3, C4, C5, C6, C7, C8, C9, C10 | CAP ALSMD 6.6MM H7.7MM | C_POL | 10
100nF | Capacitor | C11, C13, C14, C18 | CAP 0603_1608 RF | C | 4
1uF | Capacitor | C12 | CAP 0603_1608 RF | C | 1
10uF | Generic Capacitor | C15, C16 | CAP 1206_3216 | C | 2
47pF | Capacitor | C19 | CAP 0603_1608 RF | C | 1
HLMP-3507 | Green 5mm TH LED, T-1 3/4, 10mA Ic, 2.1V | D1, D2, D5 | LED TH 5mm | LED_TH5_GREEN | 3
HLMP-3301 | Red 5mm TH LED, T-1 3/4, 10mA Ic, 1.9V | D3 | LED TH 5mm | LED_TH5_RED | 1
1N4148WS-7-F | Signal Diode VR=75V IF=150mA Trr=4ns P=200mW | D4 | SOD323 | 1N4148 | 1
1054500101 | Conn USB 3.1 Type C F 24 POS Solder RA SMD 24 Terminal 1 Port USB 3.1 T/R | J1 | Molex 1054500101 - With Model | 1054500101 | 1
105313-1206 | Nano-Fit Right Angle Header; Through Hole; 2.50mm; Single Row; 6 Circuit; Gold Plated | J2 | MOLEX 1053131106 | Nano-Fit RA TH 6 Way Header | 1
5015 | PC TEST POINT MINIATURE | J3, J4, J5, J6, J7 | FP-5015-MFG-RF | 5015 | 5
62001011821 |  | J10, J11 | 62001011821 | CMP-1502-01210-2 | 2
2N7002,215 | MOSFET N-CH 60V 300MA SOT-23 | Q1 | NEXPERIA SOT-23-3 | 2N7002 | 1
560R | Resistor | R1 | RES 0603_1608 RF | R | 1
240R | Resistor | R2 | RES 0603_1608 RF | R | 1
330R | Resistor | R3 | RES 0603_1608 RF | R | 1
10k | Resistor | R4, R5, R6 | RES 0603_1608 RF | R | 3
180k | Resistor | R7 | RES 0603_1608 RF | R | 1
1k | Resistor | R8, R17 | RES 0603_1608 RF | R | 2
680k | Resistor | R9 | RES 0603_1608 RF | R | 1
120R | Resistor | R10, R16 | RES 1206_3216 RF | R | 2
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

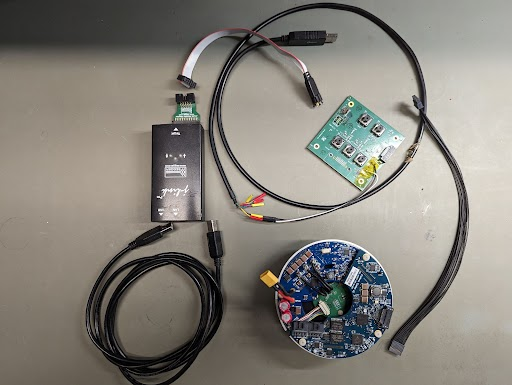
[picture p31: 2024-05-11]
docs/images/robot_assembly/single_motor/motor_parts.png

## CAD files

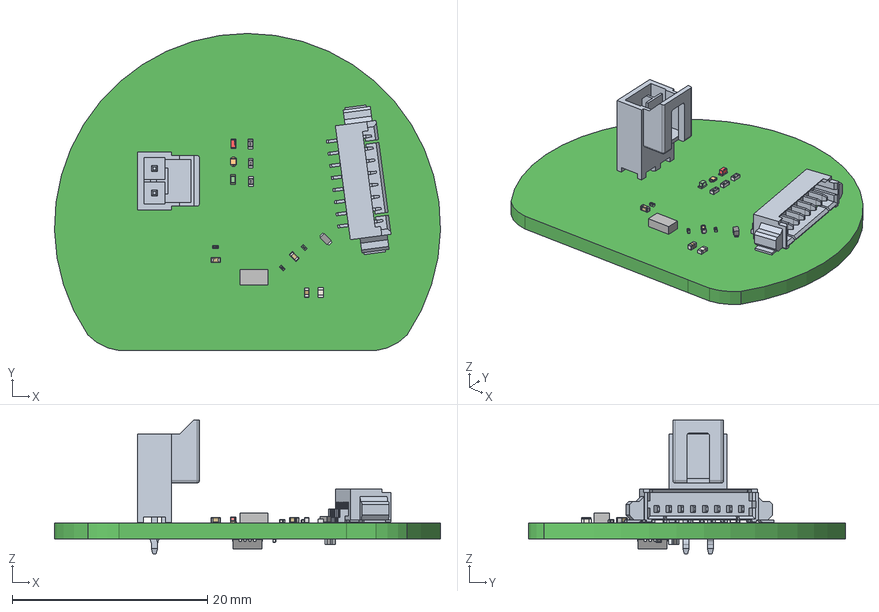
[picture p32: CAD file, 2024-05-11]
hardware/electronics/ada/Project Outputs for Ada/ExportSTEP/Ada.step
39.5 x 32.4 x 13.7 mm
Extruded x 4
terminals x 2
value
Panasonic ERJ-2RKF26R7X 1 - Copy x 3
Panasonic ERJ-2RKF26R7X 1 - Copy (2) x 3
Panasonic ERJ-2RKF26R7X 1 x 3
Panasonic ss x 3
Topcover
mark
base
lens
cathode mark
logo
side x 8
Samsung logo x 4
Pins
term1
term2
name x 2
10114830-xxx08lfc
QFN17P50_300X300X100L40X24T165N

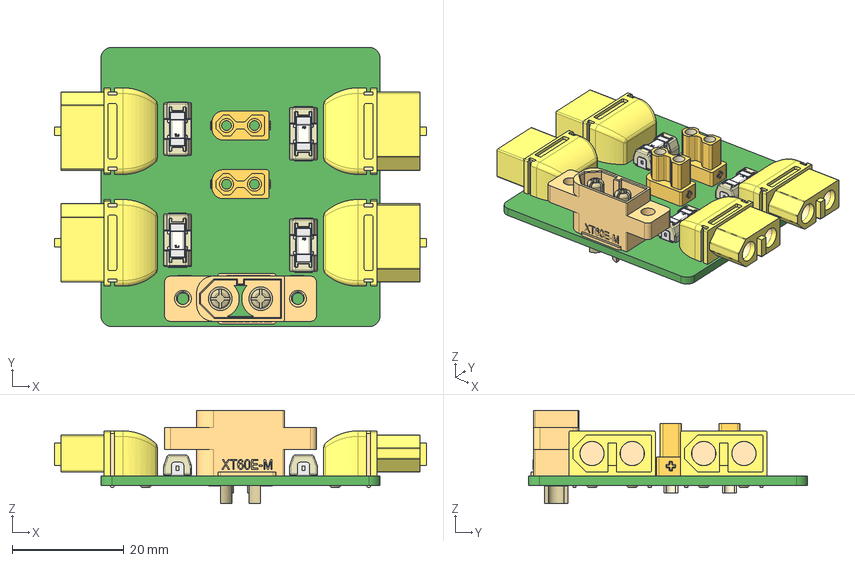
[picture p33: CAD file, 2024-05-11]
hardware/electronics/feifei/Project Outputs for Power_Distro/ExportSTEP/Fei-Fei.step
66.6 x 50.0 x 16.6 mm
logo x 4
Part Studio 1 - XT30U-F x 2
XT60PW FEMALE x 4
XT60E-M - XT60E-M

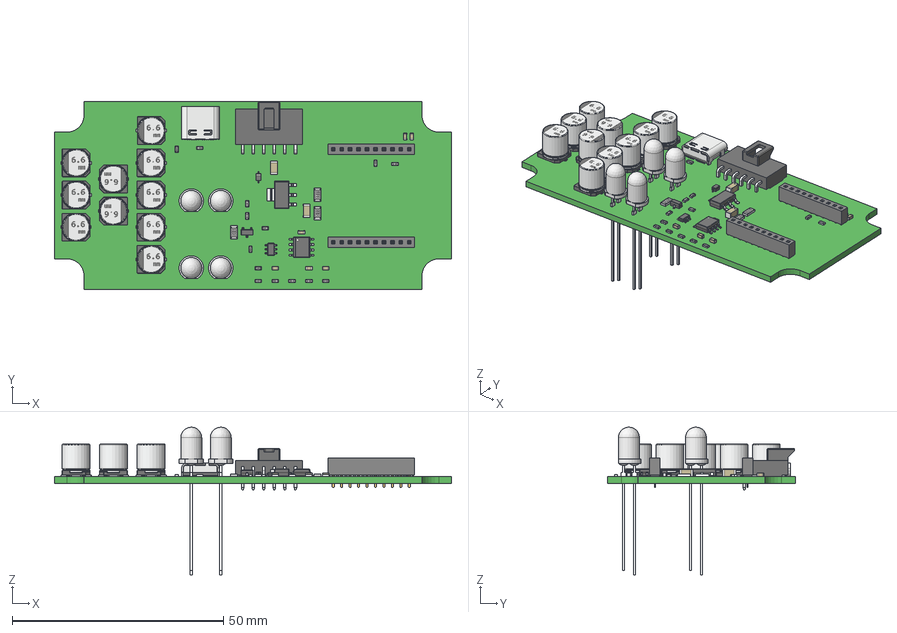
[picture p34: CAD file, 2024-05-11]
hardware/electronics/grace/Project Outputs for Grace/ExportSTEP/Grace.step
94.0 x 44.5 x 35.0 mm
6200xx11821 x 20
0603 resistor x 14
1206 resistor x 3
sot-23-3-nxp
WL-TMRW_5mm x 4
0603 cap x 6
1206 cap x 2
SOT-223
CAP ALSMD - 6.6 x 6.6 x 7.7 x 10
SOD-323
Molex - 1053131106 v1
Analog TSOT-23-6
TI - SOIC-8 - D008A v3
Molex - 1054500101 v7

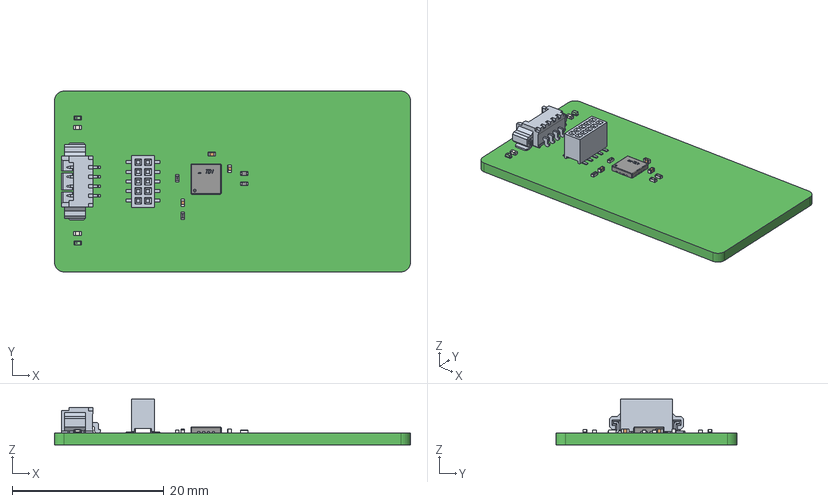
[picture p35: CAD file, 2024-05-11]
hardware/electronics/hamilton/Project Outputs for Hamilton/ExportSTEP/Hamilton.step
47.0 x 23.9 x 6.06 mm
terminals x 2
alumina substrate x 2
coating x 2
logo x 2
Panasonic ERJ-2RKF26R7X 1 - Copy x 2
Panasonic ERJ-2RKF26R7X 1 - Copy (2) x 2
Panasonic ERJ-2RKF26R7X 1 x 2
Panasonic ss x 2
side x 6
Murata x 3
color x 2
Extruded x 6
20021321-1010xxlfc
pads
FTDI Logo

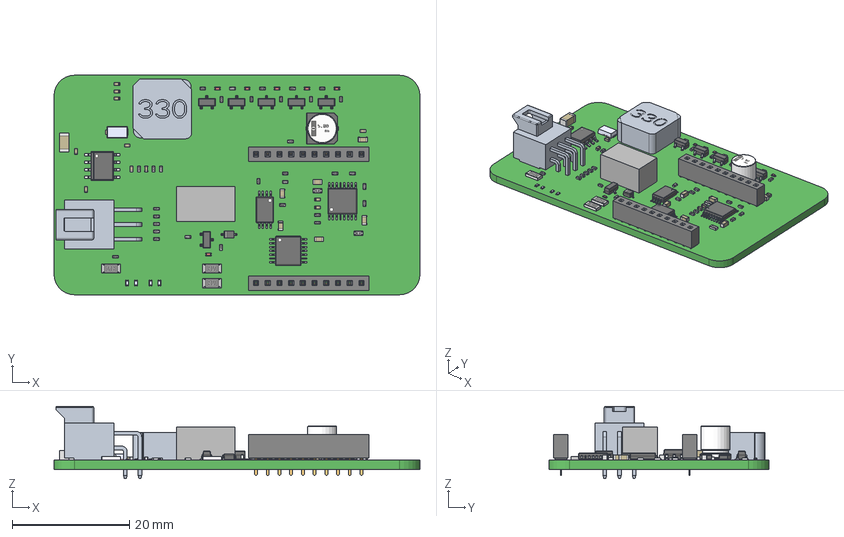
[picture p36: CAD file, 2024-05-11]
hardware/electronics/hopper/Project Outputs for Hopper/ExportSTEP/Hopper.step
62.5 x 37.5 x 12.3 mm
6200xx11821 x 20
0603 cap x 6
0402 resistor x 32
sot-23-3-nxp x 6
SRR1050A-180Y
SMP Package
0402 cap x 11
1206 cap
TSSOP-14
LED 0402 Lens RED x 6
LED 0402 Base RED x 6
0603 resistor x 2
TI - SOIC-8 - D008A v3
TSSOP-16-TI-PW
TSSOP-8
1206 resistor x 3
Extruded
SOD-323
LED 0402 Lens GREEN x 4
LED 0402 Base GREEN x 4

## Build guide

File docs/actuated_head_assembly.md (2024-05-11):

# Barkour Robot Actuated Head Assembly

This document describes the assembly instructions for the actuated head.

The actuated head adds 2 degrees of freedom to the robot's neck as well as a
mouth (gripper). In this hardware variant, the Intel RealSense camera is removed
and image/depth data is instead provided by RGB and ToF sensors located in the
robot's eye sockets.

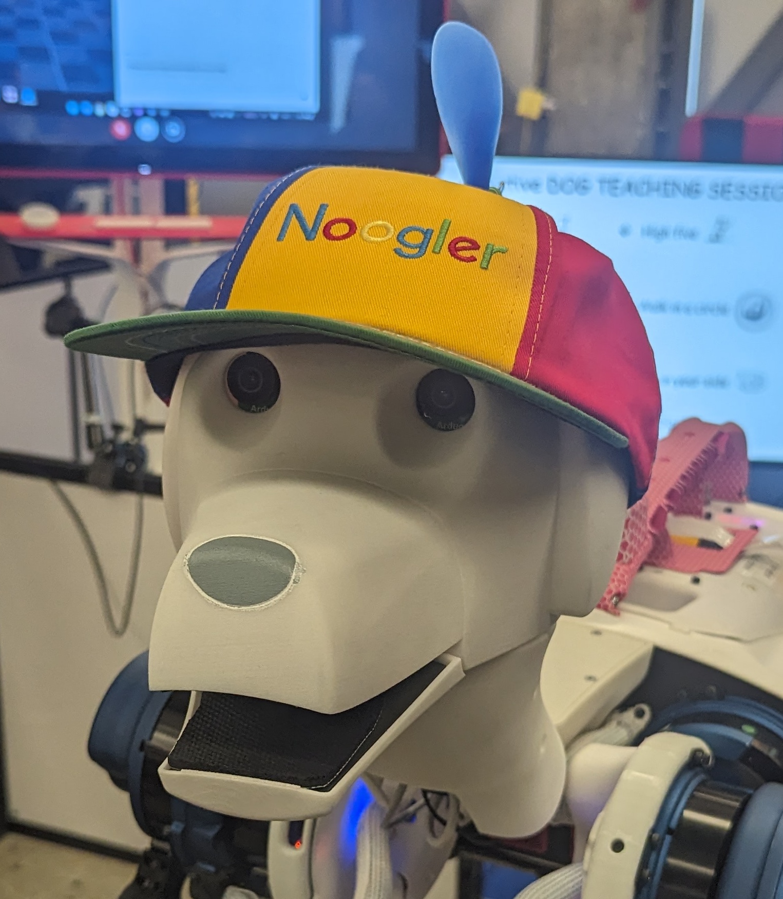
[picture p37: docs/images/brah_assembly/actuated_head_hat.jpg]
Actuated head


### Neck Base Structure

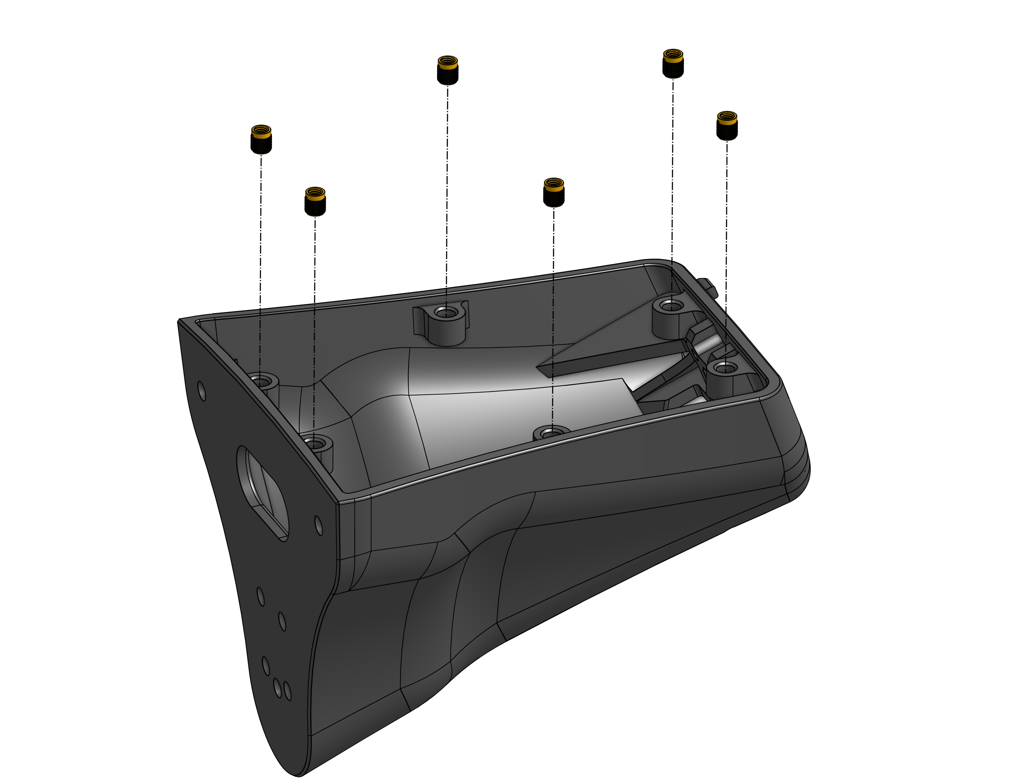
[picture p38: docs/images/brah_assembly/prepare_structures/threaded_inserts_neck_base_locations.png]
neck structure threaded insert locations


#### Parts Required

Prepare the following parts:

Qty | Part No.  | Description
--- | --------- | --------------------------------------------
6   | 94510A030 | M3x0.5, 4.8mm long expanding threaded insert

Prepare the following tools:

Qty | Tool  | Where used | Torque?
--- | ----- | ---------- | -------
1   | Punch | Step 2     | N/A

#### Instructions

1.  Partially place expanding inserts into all six holes by hand, as shown:

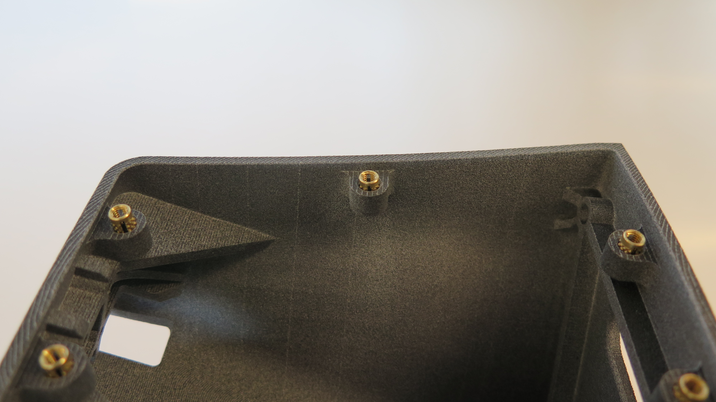
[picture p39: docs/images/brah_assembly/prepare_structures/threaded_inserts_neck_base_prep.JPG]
neck structure threaded insert prep


1.  Using a flat-faced punch, firmly press the insert into the hole until the
    top edge is flush with the part face, as shown: {value=2}

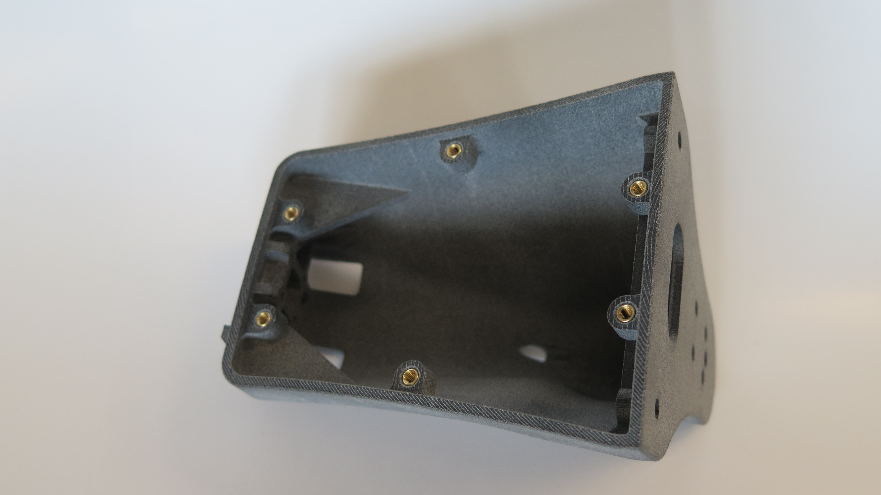
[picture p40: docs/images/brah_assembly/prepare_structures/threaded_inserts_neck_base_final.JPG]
neck structure threaded insert final


### Neck Base Cover Structure

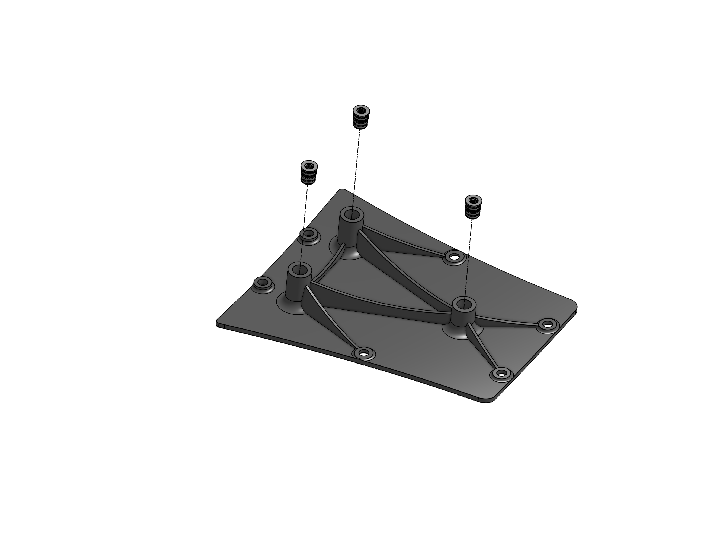
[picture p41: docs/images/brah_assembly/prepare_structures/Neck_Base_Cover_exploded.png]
neck base cover structure threaded insert locations


#### Parts Required

Prepare the following parts:

Qty | Part No.  | Description
--- | --------- | --------------------------------------------
3   | 94510A030 | M3x0.5, 4.8mm long expanding threaded insert

Prepare the following tools:

Qty | Tool  | Where used | Torque?
--- | ----- | ---------- | -------
1   | Punch | Step 2     | N/A

#### Instructions

1.  Partially place expanding inserts into both holes by hand, as shown:

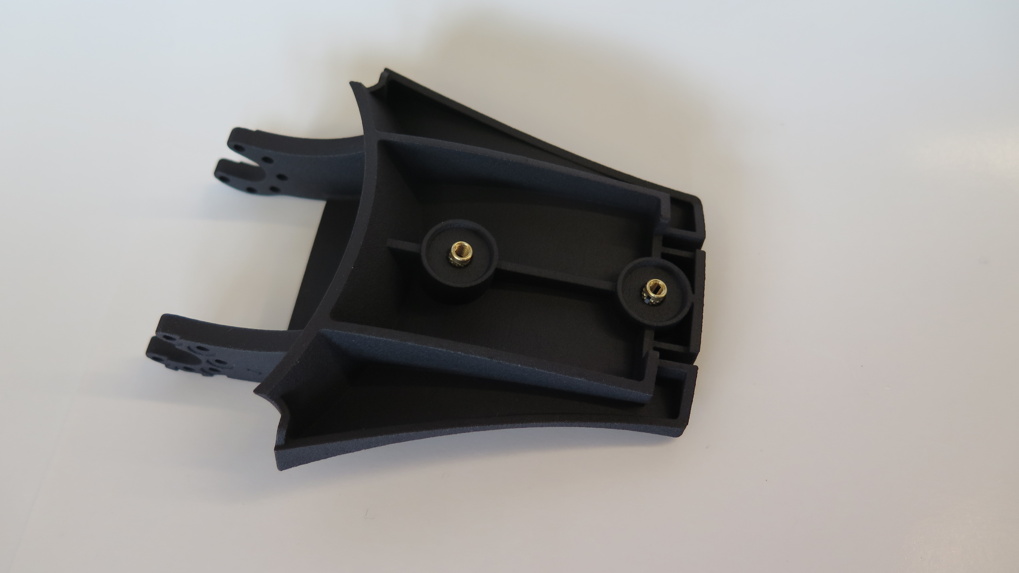
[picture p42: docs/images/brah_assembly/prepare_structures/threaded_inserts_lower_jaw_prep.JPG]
lower jaw structure threaded insert prep


1.  Using a flat-faced punch, firmly press the insert into the hole until the
    top edge is flush with the part face, as shown: {value=2}

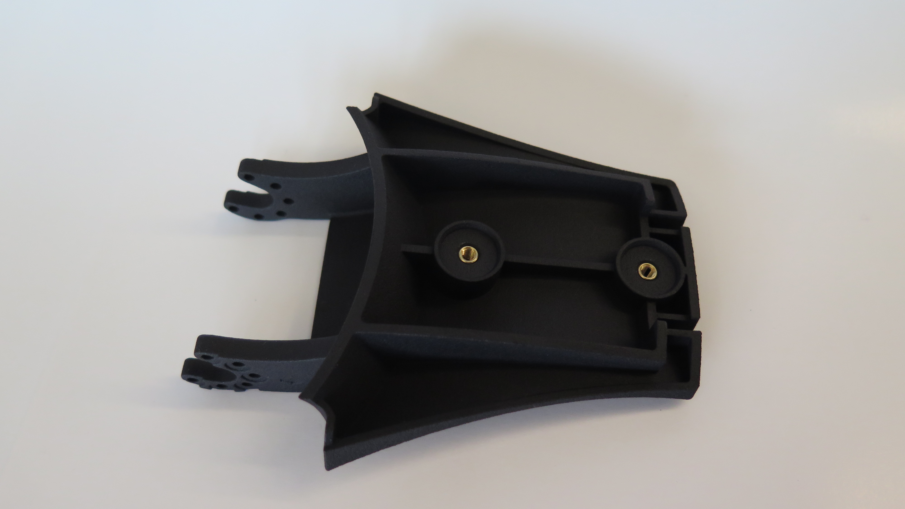
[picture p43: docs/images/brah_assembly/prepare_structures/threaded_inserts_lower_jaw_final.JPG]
lower jaw structure threaded insert final


### Neck Structure

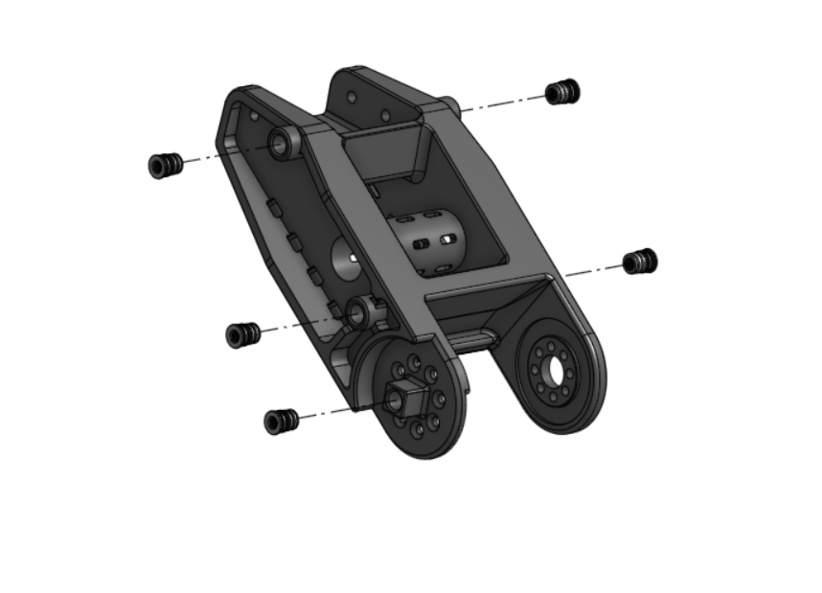
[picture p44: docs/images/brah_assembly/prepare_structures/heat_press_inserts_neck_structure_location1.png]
neck structure heat press insert locations


#### Parts required

Prepare the following parts:

Qty | Part No.  | Description
--- | --------- | --------------------------------------------
5   | 94180A333 | M3x0.5,6.4mm long heat press threaded insert

Prepare the following tools:

Qty | Tool                                  | Where used | Torque?
--- | ------------------------------------- | ---------- | -------
1   | M3 Heat Insert press tip              | Step 1     | N/A
1   | Temperature controlled soldering iron | Step 2     | N/A

#### Instructions

WARNING: Soldering irons are hot. Be aware of both burn and fire hazards.

1.  Install the M3 heat insert press tip into a temperature controlled soldering
    iron.
2.  Set the iron's temperature to 140C.
3.  Gently press the heat press insert into the neck structure using the iron.
    Stop when the top surface is flush with the part. Flushed or slightly
    sub-flushed is good to avoid the flash (melted material) from interfering
    with subsequent assembly. Support the thinner flange from underneath to
    avoid excessive stress that might bend or break the part.

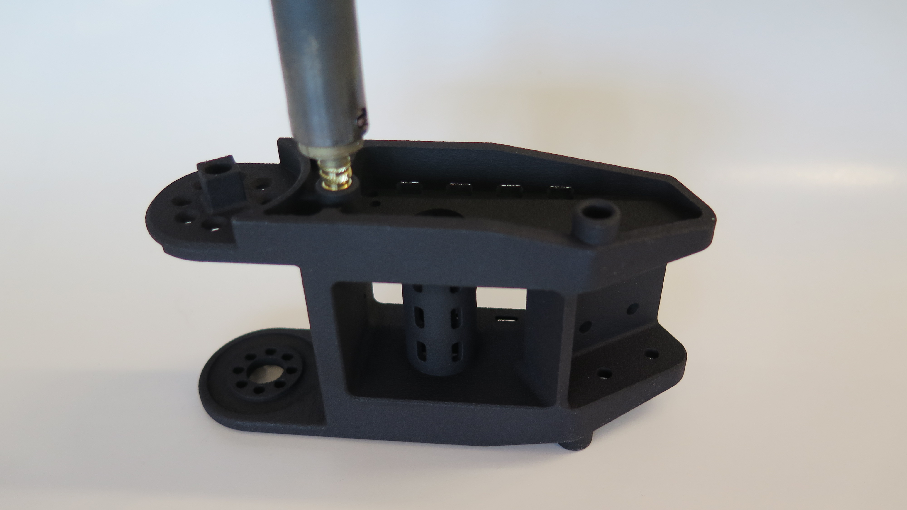
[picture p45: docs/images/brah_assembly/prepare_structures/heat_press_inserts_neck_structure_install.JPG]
neck structure heat press insert install

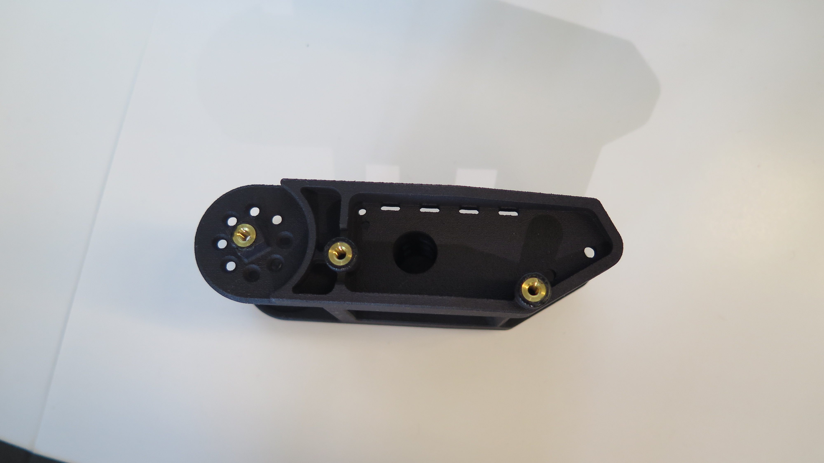
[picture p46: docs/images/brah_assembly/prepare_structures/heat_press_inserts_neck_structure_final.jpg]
neck structure heat press insert final


### Head Structure

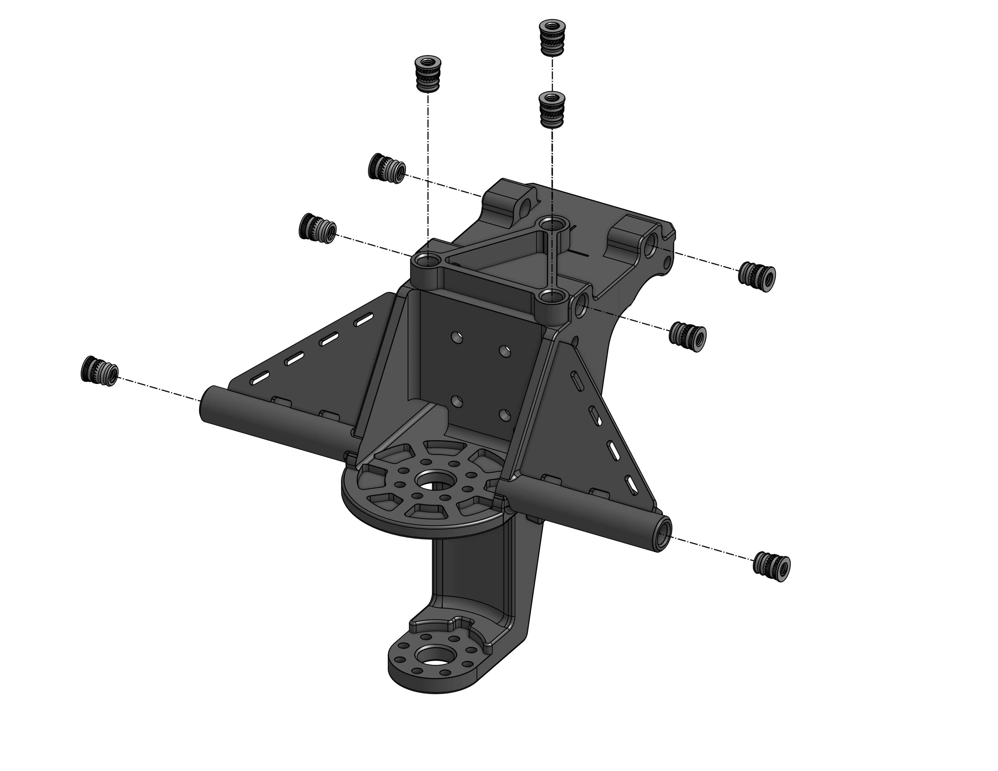
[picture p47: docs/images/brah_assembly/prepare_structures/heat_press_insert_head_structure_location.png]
head structure heat press insert locations


#### Parts required

Prepare the following parts:

Qty | Part No.  | Description
--- | --------- | --------------------------------------------
9   | 94180A333 | M3x0.5,6.4mm long heat press threaded insert

Prepare the following tools:

Qty | Tool                                  | Where used | Torque?
--- | ------------------------------------- | ---------- | -------
1   | M3 Heat Insert press tip              | Step 1     | N/A
1   | Temperature controlled soldering iron | Step 2     | N/A

#### Instructions

WARNING: Soldering irons are hot. Be aware of both burn and fire hazards.

1.  Install the M3 heat insert press tip into a temperature controlled soldering
    iron.
2.  Set the iron's temperature to 140C.
3.  Gently press the heat press insert into the neck structure using the iron.
    Stop when the top surface is flush with the part.

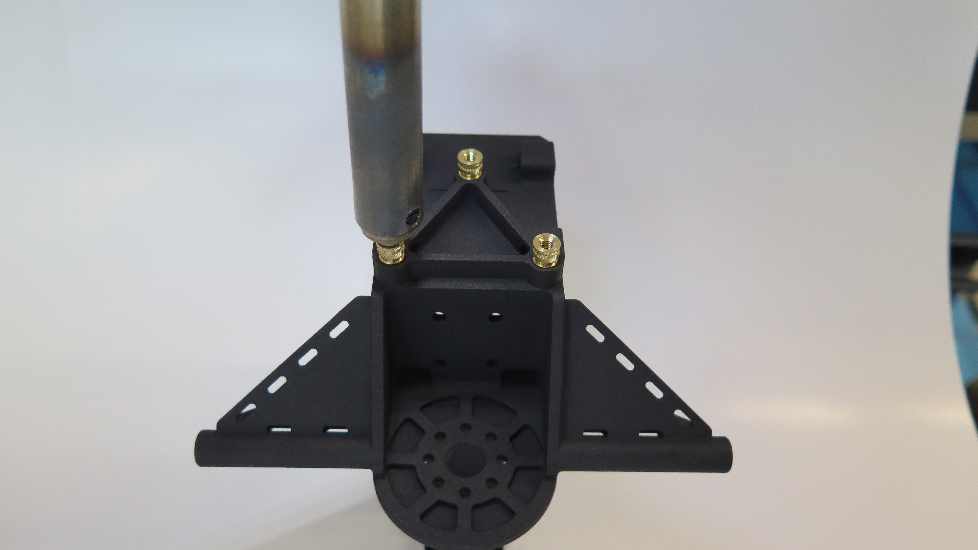
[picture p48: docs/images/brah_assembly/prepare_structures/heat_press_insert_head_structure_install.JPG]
head structure heat press insert install

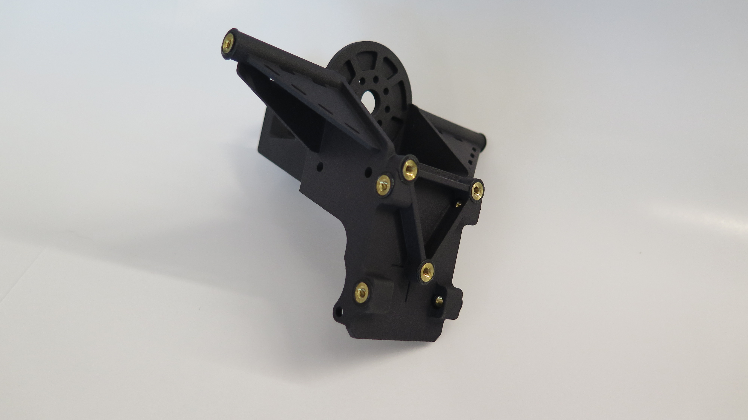
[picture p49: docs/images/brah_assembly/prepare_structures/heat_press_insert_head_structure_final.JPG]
head structure heat press insert final


#### Instructions

1.  Install the M3 heat insert press tip into a temperature controlled soldering
    iron.
2.  Set the iron's temperature to 140C.
3.  Gently press the heat press insert into the neck structure using the iron.
    Stop when the top surface is flush with the part.

neck structure heat press insert install
neck structure heat press insert final

### Shells

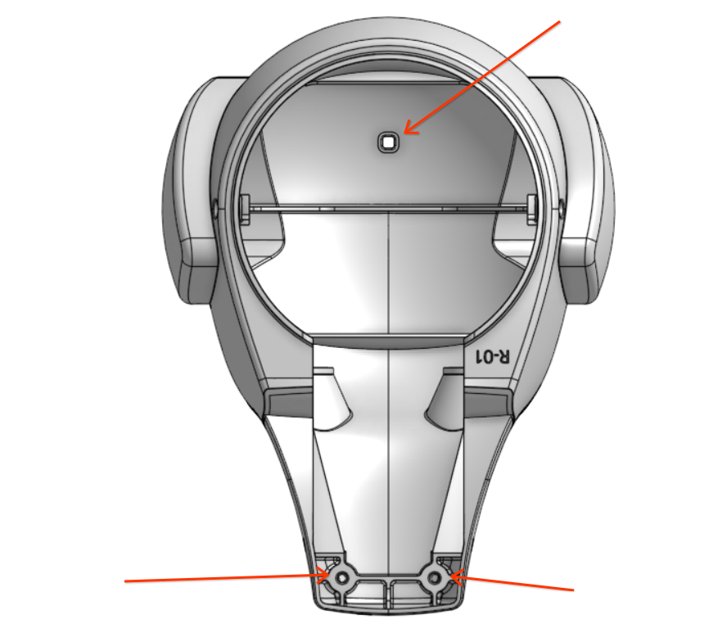
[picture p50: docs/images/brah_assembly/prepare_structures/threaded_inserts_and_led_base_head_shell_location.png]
head shell threaded insert locations

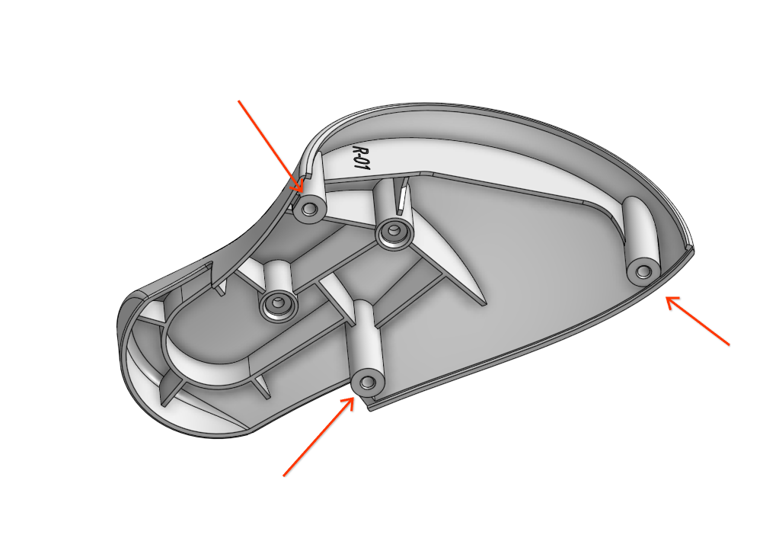
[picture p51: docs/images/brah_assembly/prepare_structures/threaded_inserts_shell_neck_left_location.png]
neck left shell threaded insert locations


#### Parts Required

Prepare the following parts:

Qty | Part No.            | Description
--- | ------------------- | --------------------------------------------
5   | 94510A030           | M3x0.5, 4.8mm long expanding threaded insert
1   | N/A                 | Head Shell
1   | N/A                 | Left Neck Shell
1   | N/A                 | Right Neck Shell
1   | SZ1-6.00-RGB-F4PD-9 | SZ1-6.00-RGB-F4PD Light Pipe

Prepare the following tools:

Qty | Tool                  | Where used | Torque?
--- | --------------------- | ---------- | -------
1   | Punch                 | Step 1     | N/A
1   | xacto blade           | Step 2     | N/A
1   | Dark permanent marker | Step 4     | N/A

#### Instructions

1.  Using a flat-faced punch, firmly press the insert into the hole until the
    top edge is flush with the part face, as shown: {value=1}

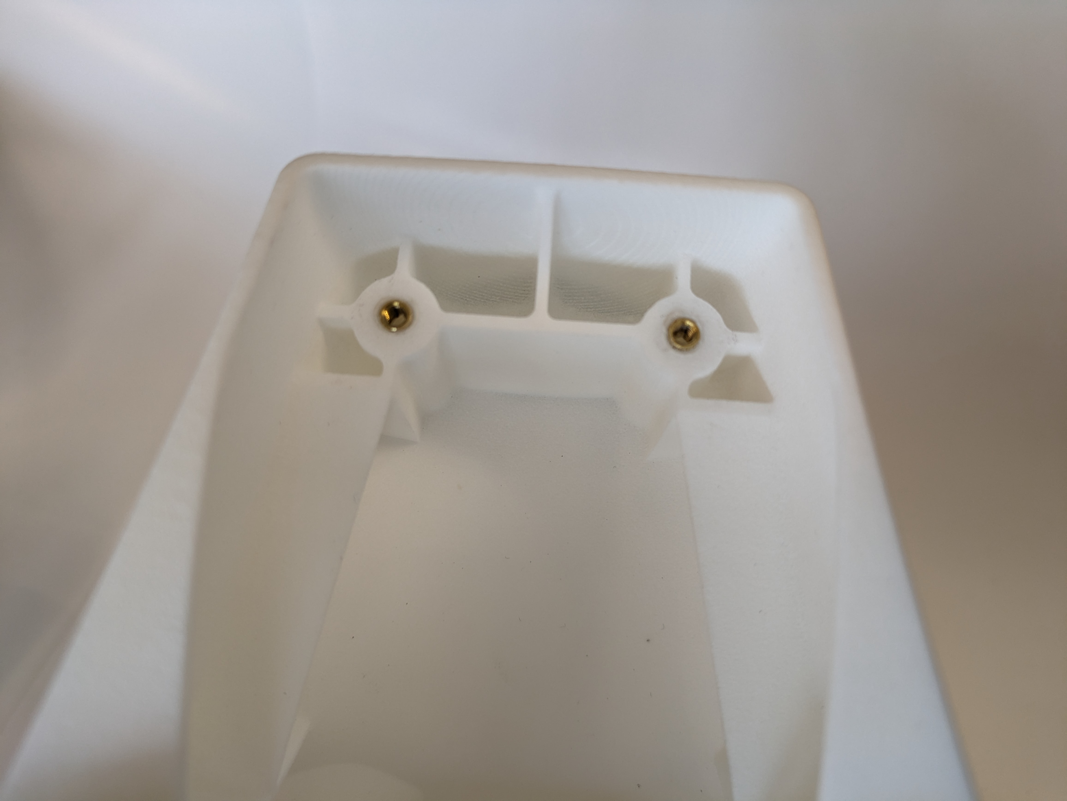
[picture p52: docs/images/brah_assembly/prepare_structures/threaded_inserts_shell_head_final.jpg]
head shell threaded insert final

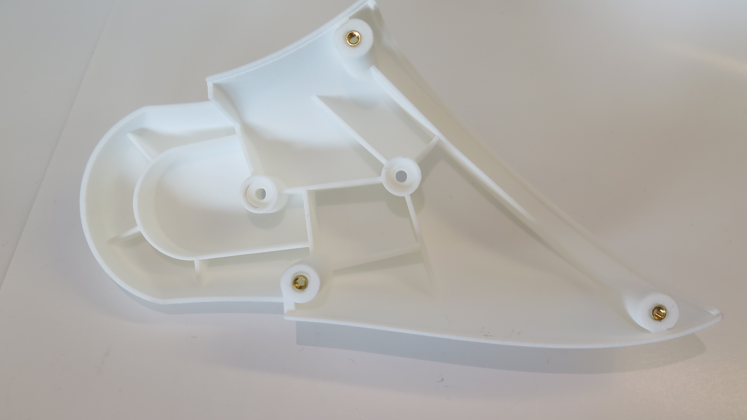
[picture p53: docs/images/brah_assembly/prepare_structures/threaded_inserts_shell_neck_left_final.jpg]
left neck threaded insert final


1.  Color the nose with the marker. {value=2}

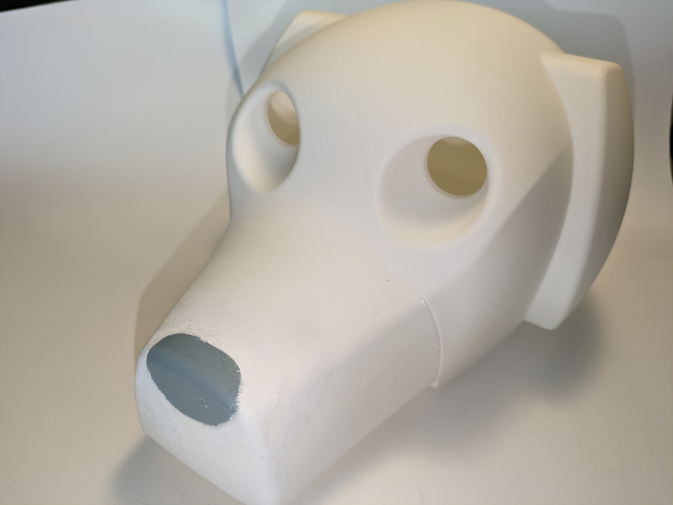
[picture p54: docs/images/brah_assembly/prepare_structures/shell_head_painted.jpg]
head on nose painted


1.  Using RT125, affix the LED base into the head shell. Allow to cure for at
    least an hour before use. Stock lightpipe is 6". Cut with scissors to 3"
    prior to bending. {value=3}

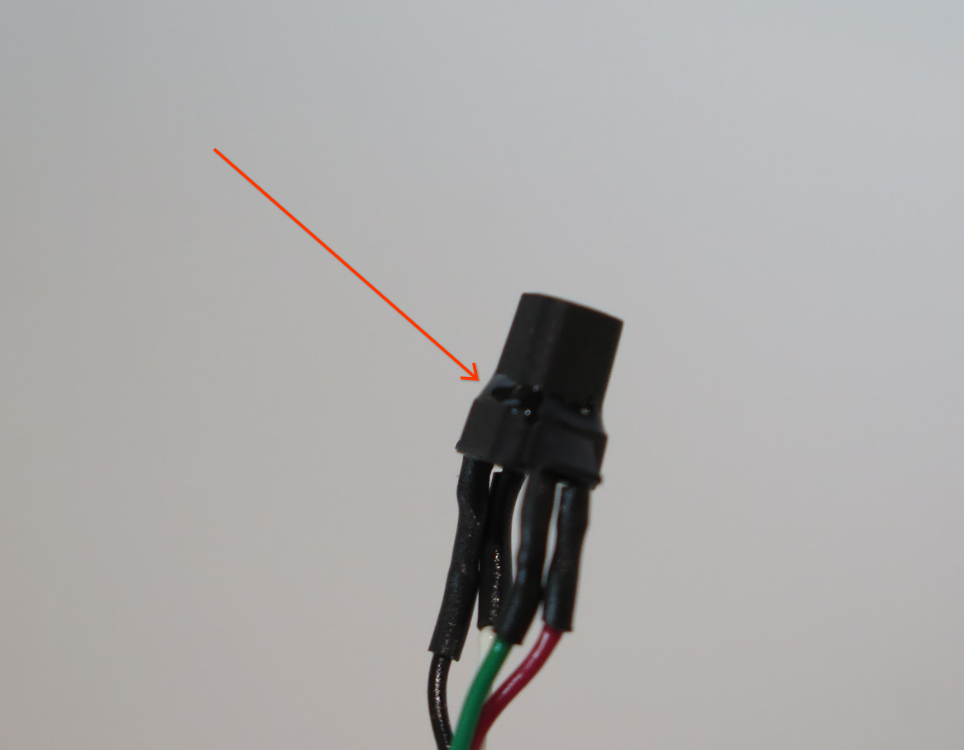
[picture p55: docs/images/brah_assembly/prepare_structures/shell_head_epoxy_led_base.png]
LED base epoxy placement

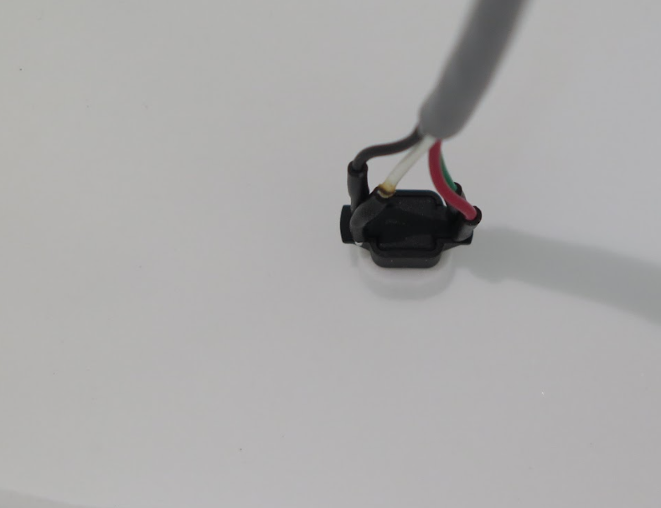
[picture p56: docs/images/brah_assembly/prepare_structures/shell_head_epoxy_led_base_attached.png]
LED base into head shell


## Subassemblies

### Dynamixel Prep

#### Requirements:

**1. Dynamixel Wizard**

Dynamixel Wizard is an optimized tool for managing Dynamixel motors from various
operating systems. In order to proceed with motor ID assignment, you will need
Dynamixel Wizard installed onto your machine. You can find the downloadable
software and installation instructions on the
[Dynamixel Wizard website](https://emanual.robotis.com/docs/en/software/dynamixel/dynamixel_wizard2/).

**2. U2D2 Connector Assembly**

The U2D2 connector assembly is a small size USB communication converter that
enables to control and to operate the DYNAMIXEL with the PC.

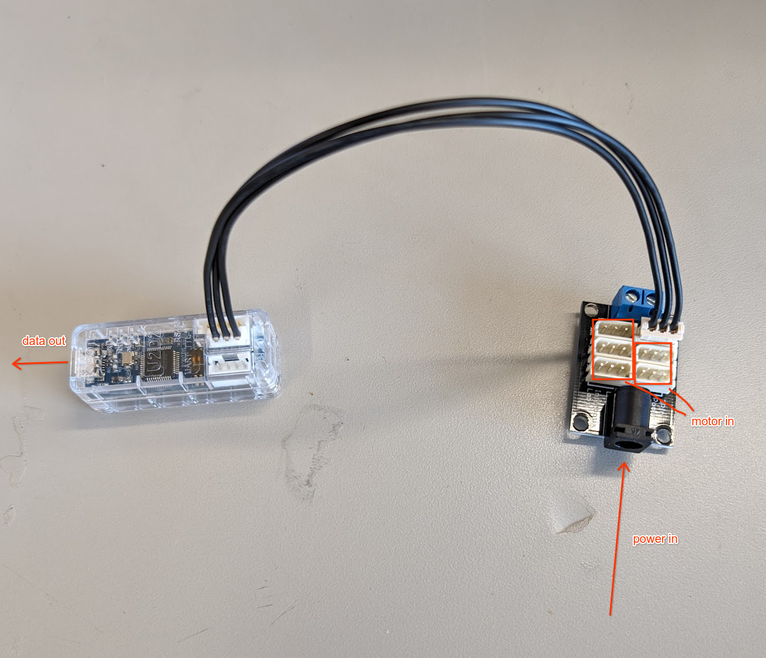
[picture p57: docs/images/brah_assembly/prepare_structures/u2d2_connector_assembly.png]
u2d2 connector assembly


#### ID Assignment

1.  Run the Dynamixel Wizard

2.  In **Options > Scan**, ensure that all of the protocols, baudrates, and
    ports are enabled prior to scanning. Lower the **ID range** to make the
    scanning process faster.

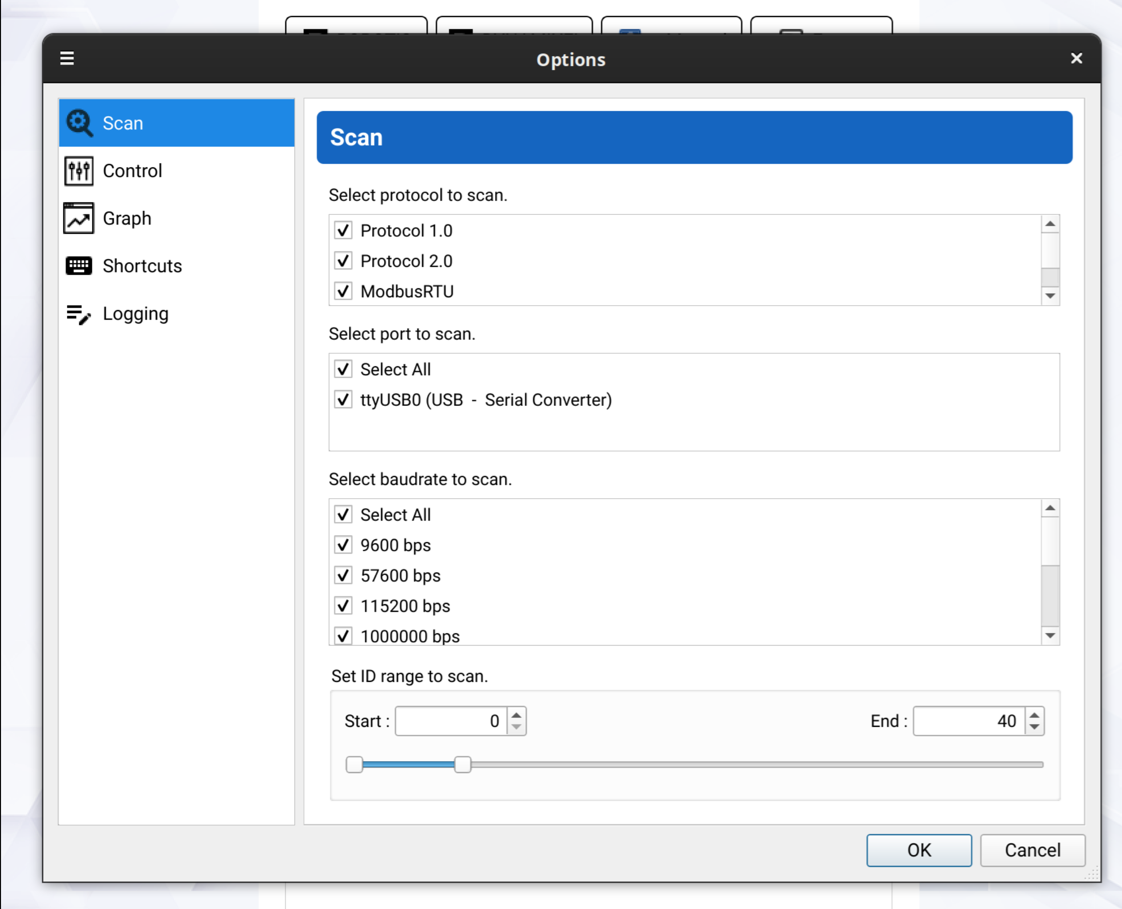
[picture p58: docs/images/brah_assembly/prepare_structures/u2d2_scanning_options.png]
Scanning Options


1.  Ensure the U2D2 assembly has power and a data connection to your PC. Plug
    the U2D2's JST connector into the desired Dynamixel motor. Once the
    connection has been made, begin the **Scan**. Once the Wizard locates your
    desired Dynamixel motor, you may press **skip** to safely end the scan
    before completion. {value=3}

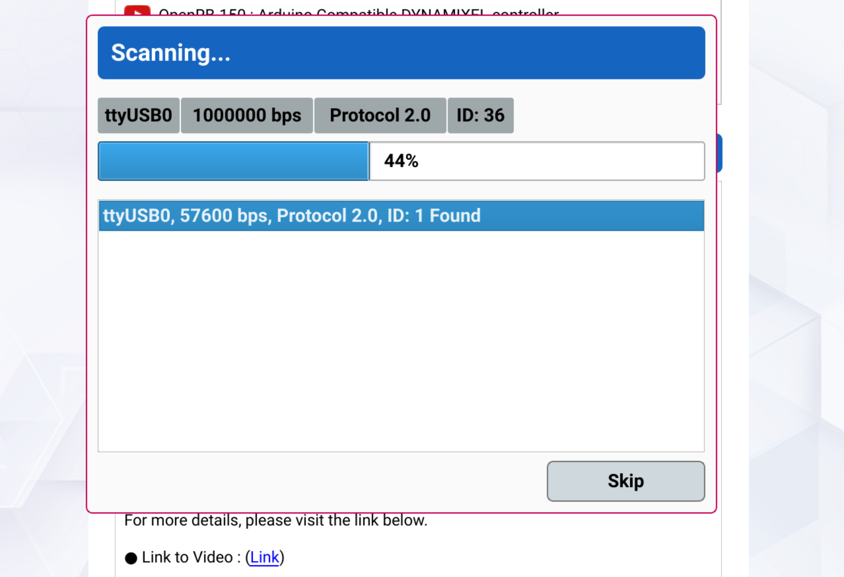
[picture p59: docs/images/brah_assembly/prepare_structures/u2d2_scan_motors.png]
Scanning for Motors


1.  **Connect** to the motor and locate **ID** in the item list. Change the
    motor's ID assignment to correspond with the motor's desired function:
    {value=4}

Function   | ID Assignment
---------- | -------------
Neck Pitch | ID 1
Head Yaw   | ID 2
Jaw        | ID 3

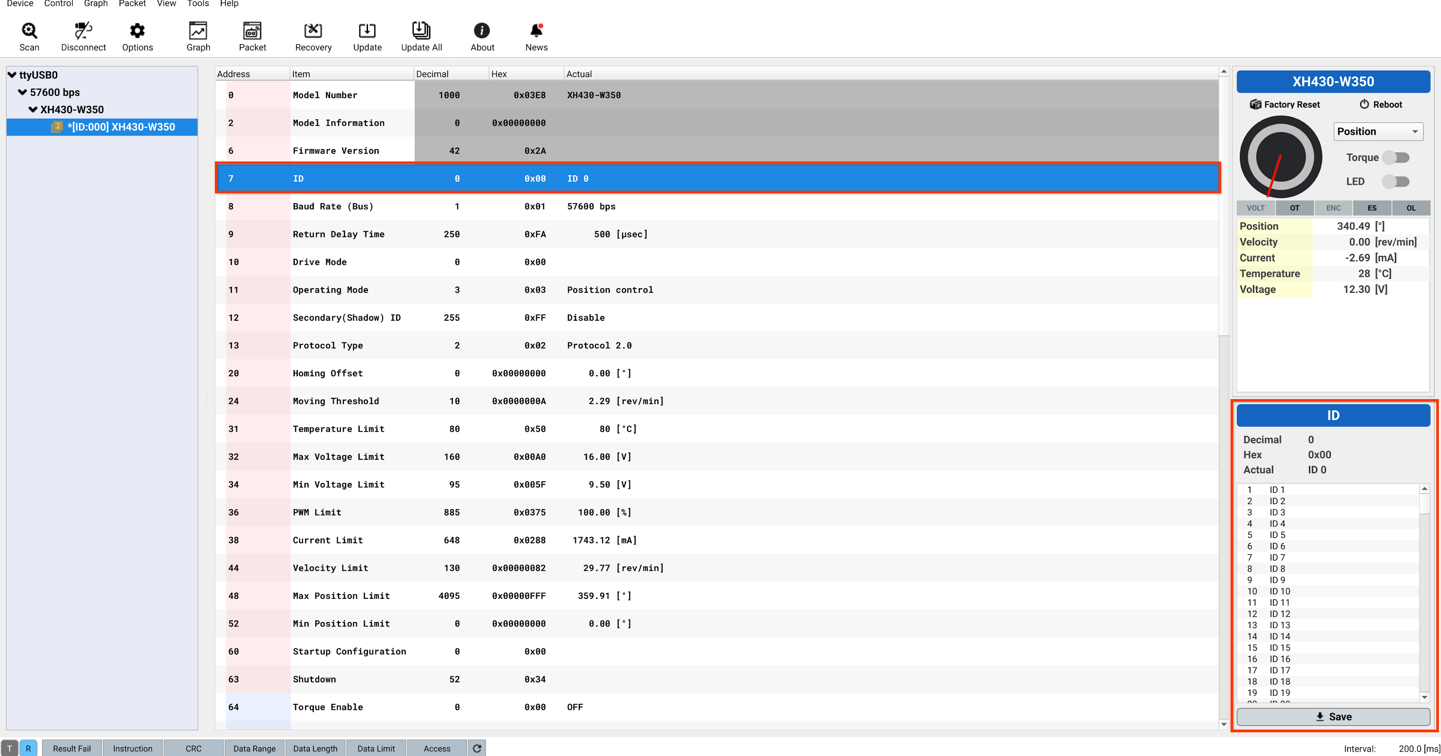
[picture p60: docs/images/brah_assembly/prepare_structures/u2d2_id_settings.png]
ID Settings


NOTE: During the motor ID assignment phase, the motors should be all be clocked
to the same orientation when looking at the absolute encoder count, such that
the programming is consistent from head unit to head unit.

NOTE: Be sure to **Save** any changes you make prior to disconnect.

1.  While you're here, now is a good opportunity to test the functionality of
    the Dynamixel motor. Enable **Torque** and mess with the dial a bit to
    ensure that the motor operates nominally. Alternatively, **Velocity** mode
    creates a smoother motion especially when testing the motors in the context
    of the head assembly. {value=5}

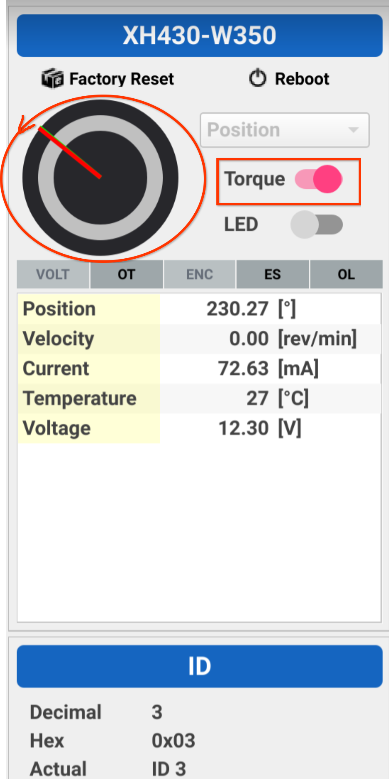
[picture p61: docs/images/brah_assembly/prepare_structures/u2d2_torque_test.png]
Torque Testing


1.  When you are done, disable **Torque** and **Disconnect** from the motor
    *before* unplugging it from the U2D2 assembly. Congratulations! You are now
    ready for assembly. {value=6}

### Dynamixel Motor Cables Subassembly

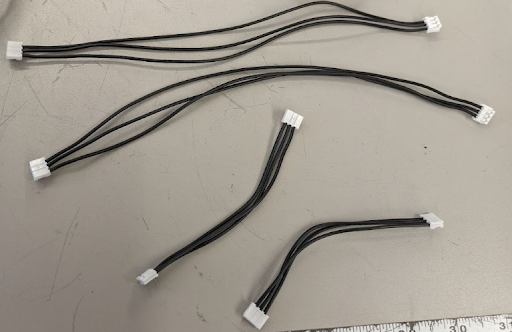
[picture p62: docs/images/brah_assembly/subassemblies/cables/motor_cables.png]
motor cables


#### Parts required

Prepare the following parts:

Qty | Part No.      | Description
--- | ------------- | --------------------------------------
6   | 2196761123    | Molex MINI SPOX 2.5 F-F 225MM 22 AWG B
4   | EHR-3         | JST CONN RCPT HSG 3POS 2.50MM
12  | SEH-001T-P0.6 | JST CONN SOCKET 22-30AWG CRIMP TIN

NOTE: 2x 225mm motor cables are being assembled for the neck pitch motor -> head
yaw motor, and the head yaw motor -> jaw motor

Prepare the following tools:

Qty | Tool                                   | Where used
--- | -------------------------------------- | ------------
1   | Wire cutter                            | Step 2, 4,
1   | Wire stripper                          | Step 3
1   | WC-260 TOOL HAND CRIMPER 22-30AWG SIDE | Step 5, 6, 7

#### Instructions

WARNING: Avoid cuts, ensure your cut direction with the blade is away from your
digits and body.

1.  Assemble the following items to make **2x of the 225mm** motor cable.
    {value=1}

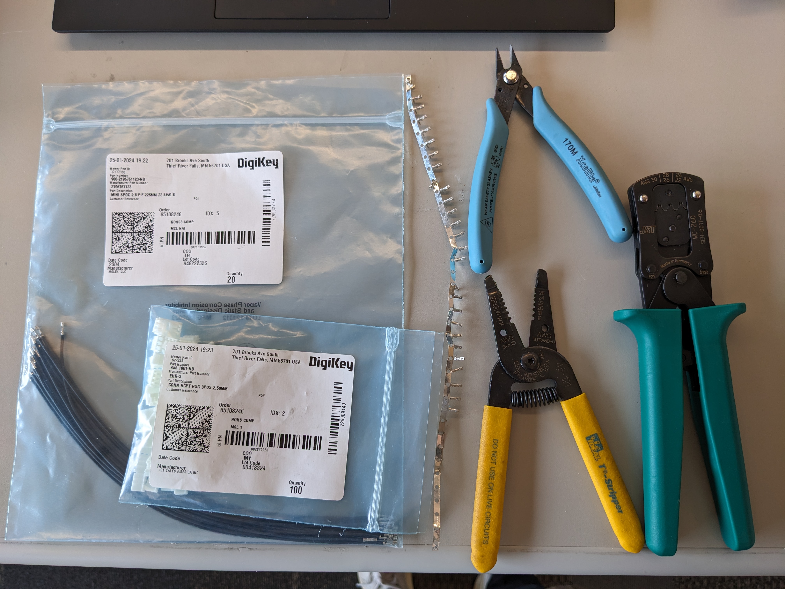
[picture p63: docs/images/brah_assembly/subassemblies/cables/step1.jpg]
image of tools for cable building


1.  Cut the crimps off the wire and ensure the wire length is the length of the
    motor cable you're intending to make (either 100 or 225mm) {value=2}

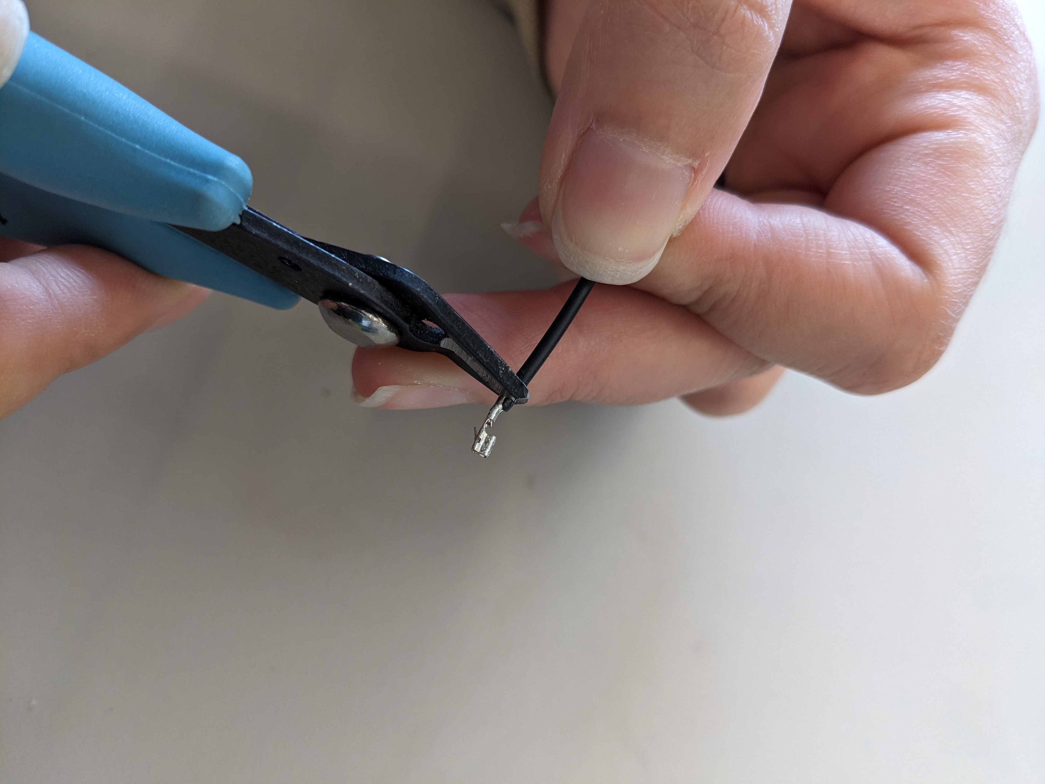
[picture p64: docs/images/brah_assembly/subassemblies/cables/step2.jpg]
image of cut off crimp


NOTE: When stripping the wire for the next step, keep in mind that the second
set of "teeth", furthest away from the tip of the connector, should bite into
the insulation of the wire and the first set, closest to the tip of the
connector, should wrap around the stripped wire

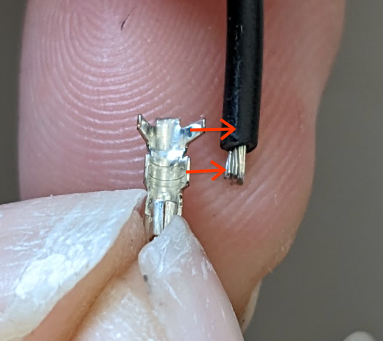
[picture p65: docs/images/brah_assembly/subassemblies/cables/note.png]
image of crimp and cable


1.  Strip ~1mm of the insulation jacket off. {value=3}

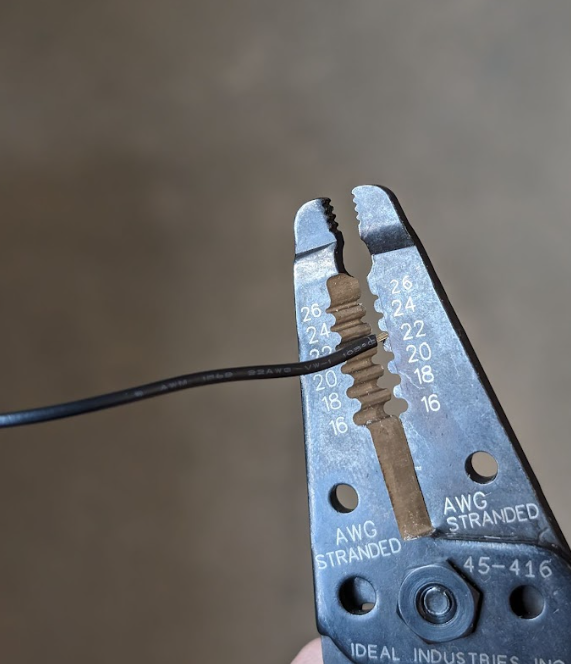
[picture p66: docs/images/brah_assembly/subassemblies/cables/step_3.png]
image of strip jacket


1.  Cut a crimp off from its bundle. {value=4}

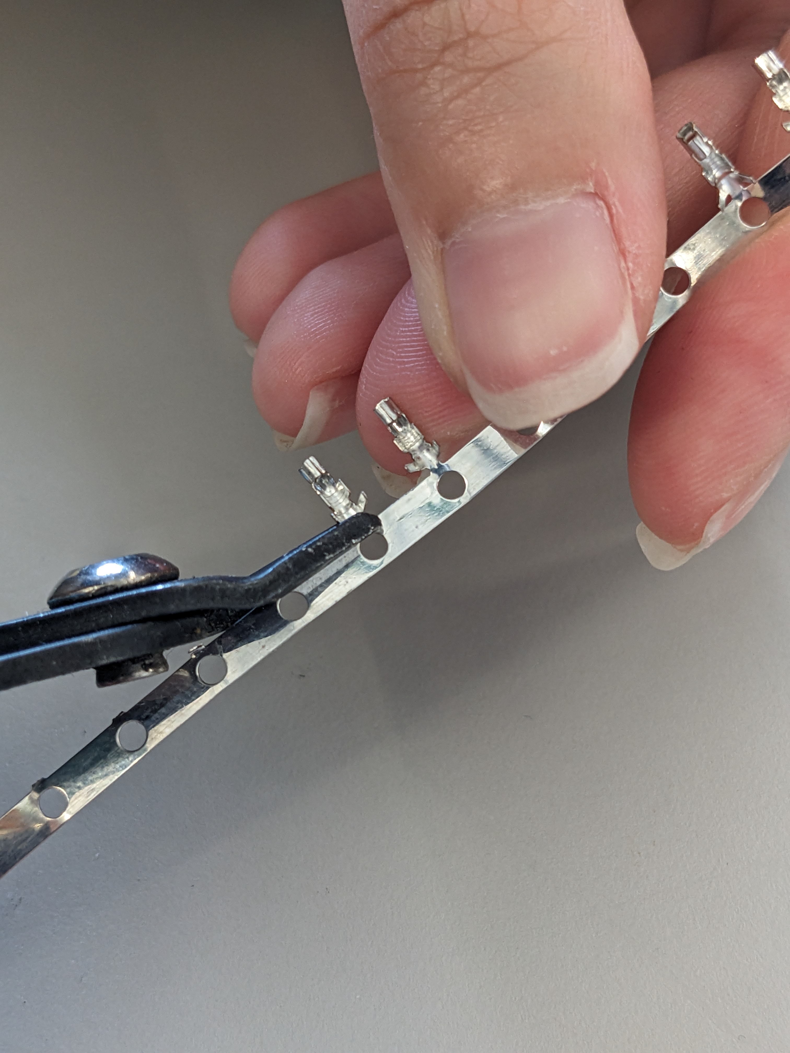
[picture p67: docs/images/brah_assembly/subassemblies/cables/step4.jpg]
image of cut crimp


1.  Pull back the crimp connector holder of the crimper and load the connector
    in. {value=5}

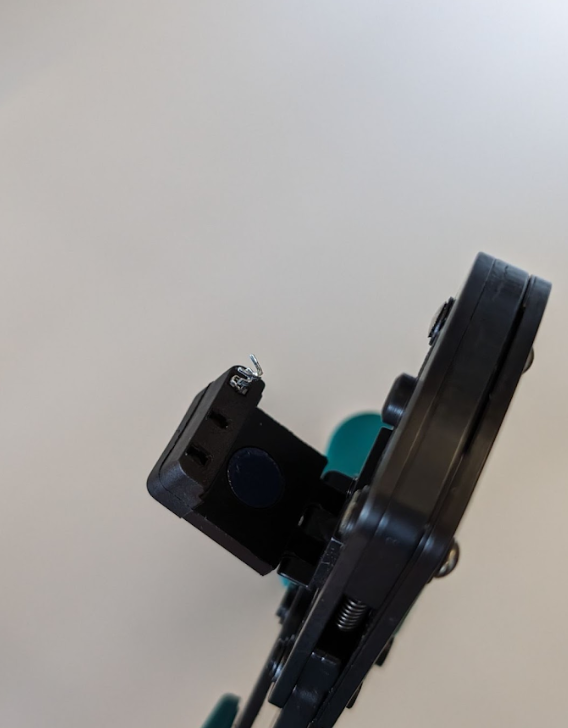
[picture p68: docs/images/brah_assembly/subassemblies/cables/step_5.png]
image of load crimp into crimper


1.  Push the holder so it sits against the crimper again and ensure the
    connector is seated as shown. {value=6}

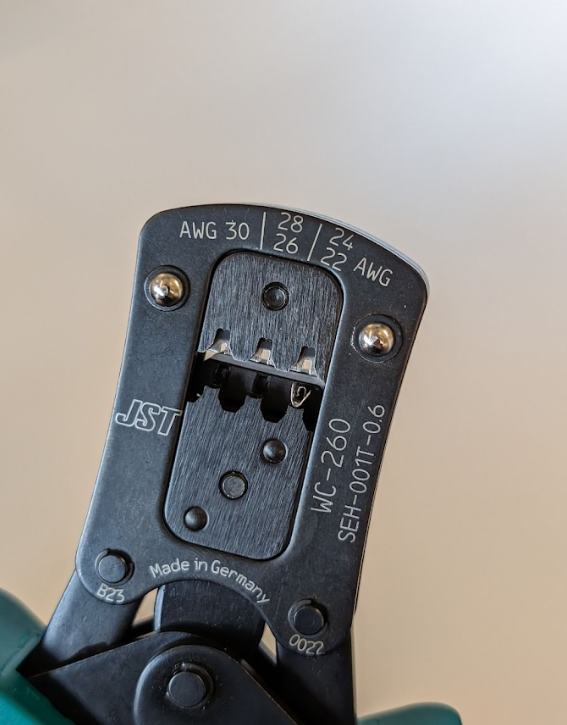
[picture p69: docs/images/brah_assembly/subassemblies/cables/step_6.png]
image of push back holderin


1.  Position the wire so that the furthest set of teeth from the tip of the
    connector bite into the insulation jacket and the closest set of teeth from
    the tip of the connector wrap around the stripped wire, and crimp the wire
    {value=7}

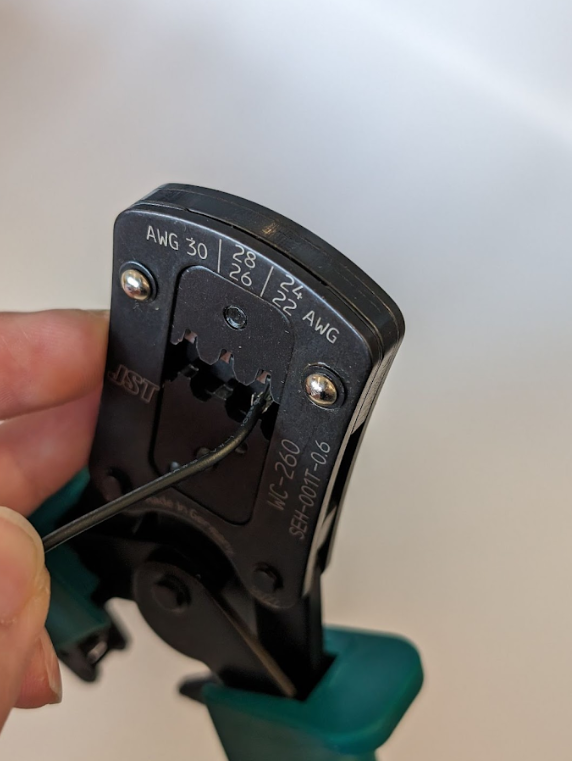
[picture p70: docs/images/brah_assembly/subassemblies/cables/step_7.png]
image of load crimp into crimper


1.  Confirm that the wire crimped successfully and repeat Step 2 to 7 two more
    times so that there are 3 wires total {value=8}

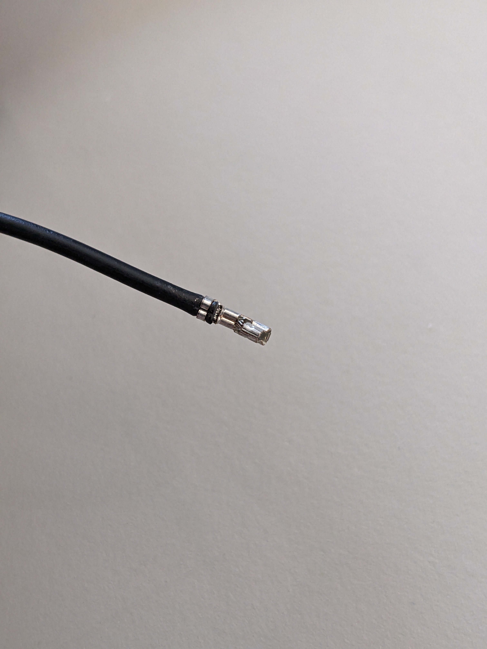
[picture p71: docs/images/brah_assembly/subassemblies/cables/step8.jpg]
image of crimped wire


1.  Line up the 3 crimped wires with 2 JST connector on each end {value=9}

image of assembling cable

1.  Insert each wire into a slot of the JST connector with the clip facing up
    and the JST connector oriented as shown below. The crimp should hook into
    place and can't be easily pulled out when seated correctly {value=10}

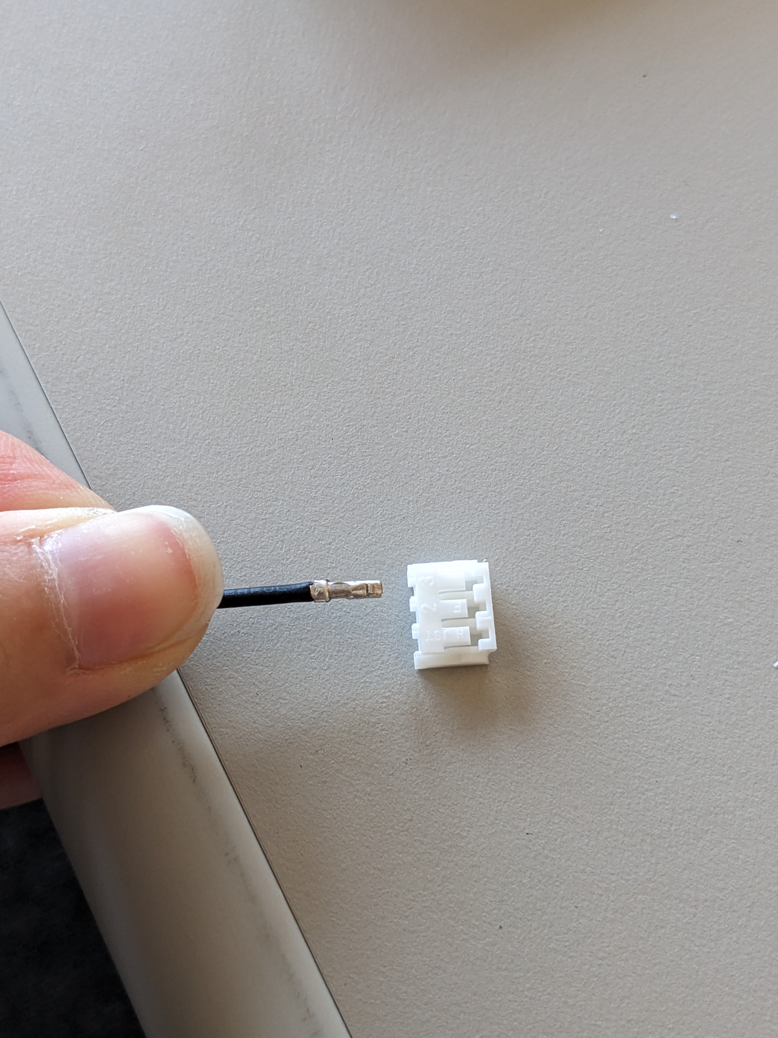
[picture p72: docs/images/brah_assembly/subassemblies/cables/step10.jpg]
image of insert wire into JST connector


1.  For the second JST connector on the other end, ensure that each wire that is
    connected goes into the same slot number as it was inserted on the first JST
    connector. You may need to gently twist the wire so it goes in the correct
    orientation. {value=11}

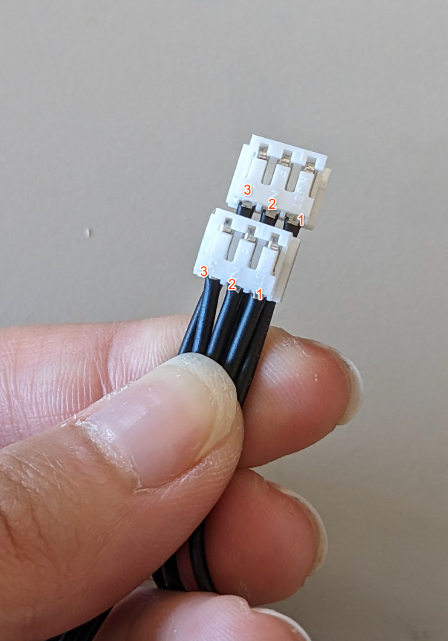
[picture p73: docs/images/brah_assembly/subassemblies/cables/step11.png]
image of confirming wires match up


1.  Ensure that the each wire of the cable is seated properly in the correct
    slot and doesn't slip out of the connector. Repeat step 2 - 11 for the other
    2 motor cables {value=12}

image of assembling cable

### Head Yaw and Jaw Motor Subassembly

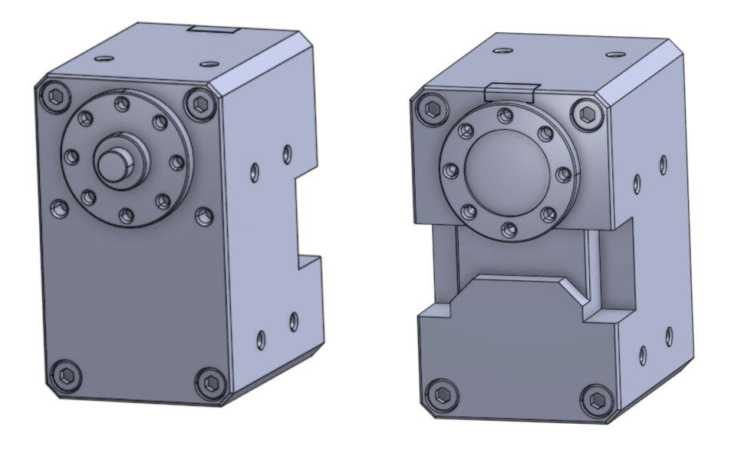
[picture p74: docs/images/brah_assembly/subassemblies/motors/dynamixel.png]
CAD of dynamixel


#### Parts required

Prepare the following parts:

Qty | Part No.     | Description
--- | ------------ | ------------------------
1   | XH430-W350-T | Dynamixel
1   | N/A          | XH430-W350-T parts kit
1   | HN12-I101    | Dynamixel idler horn kit

Prepare the following tools:

Qty | Tool                   | Where used | Torque?
--- | ---------------------- | ---------- | -------
1   | M2.0 Hex Driver bit    | Step 10    | 0.6 Nm
1   | 10-80cNm Torque Driver | Step 10    | 0.6 Nm
1   | Torque Dat tool        | Step 10    | N/A

#### Instructions

1.  Grab the idler horn (HN12-I101) and a Dynamixel to build the jaw motor:
    {value=1}

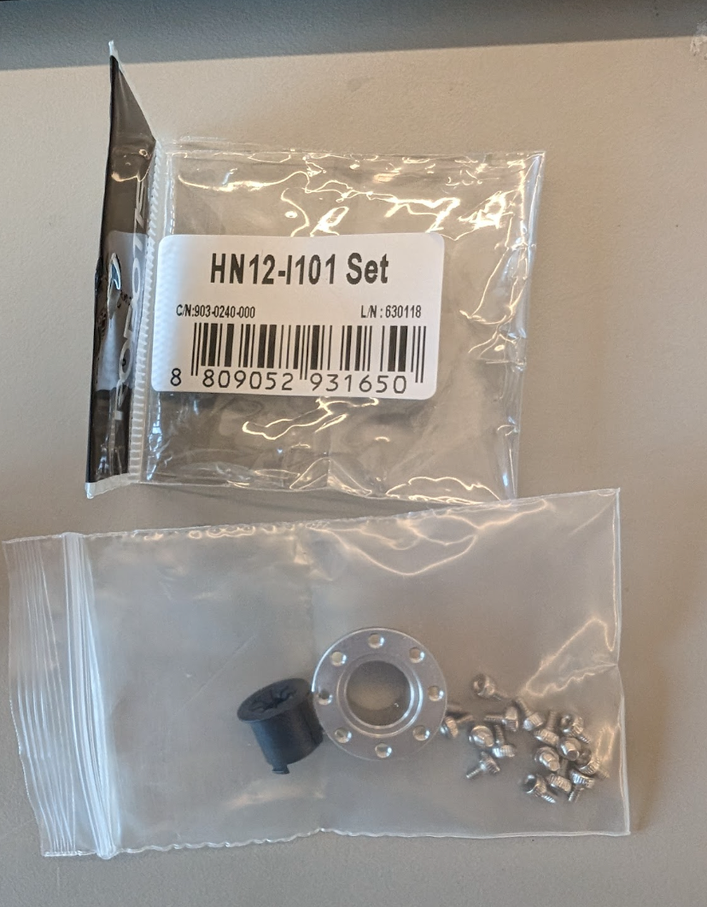
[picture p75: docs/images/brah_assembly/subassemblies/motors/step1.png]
idler horn (HN12-I101)


1.  Remove the plastic cover from the Dynamixel: {value=2}

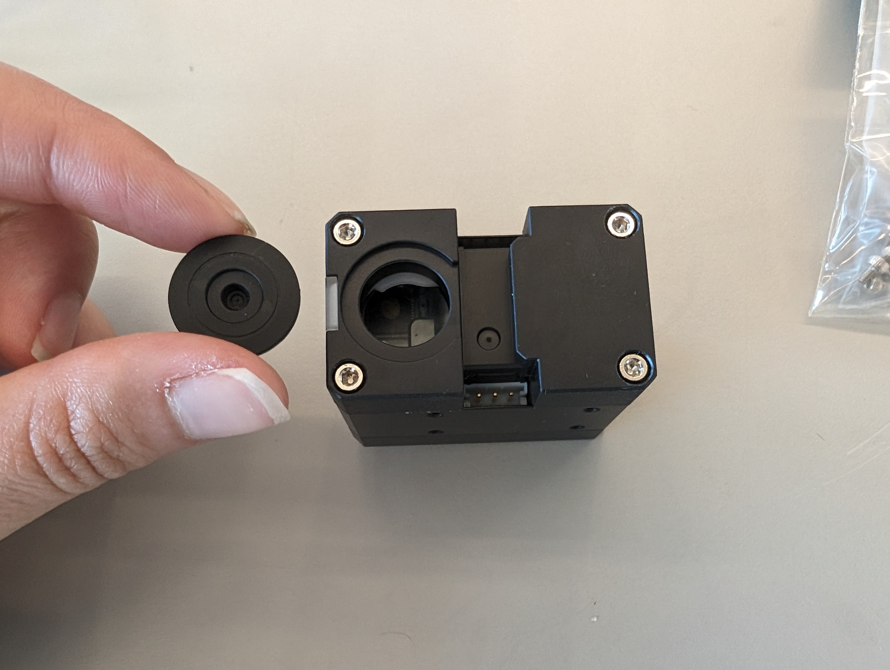
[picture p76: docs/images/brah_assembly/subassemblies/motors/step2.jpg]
image of plastic cover removed


1.  Press the beige plastic top hat bushing from the idler horn kit into the
    Dynamixel: {value=3}

image of 3 parts of idler horn

image of top hat bushing

1.  Pop the silver idler horn into the top hat bushing and it'll click when it's
    fully seated: {value=4}

image of idler horn

1.  Pop the black dust cover into the silver idler horn {value=5}

image of black dust cover

1.  Flip the dynamixel over, and use the included parts kit from the Dynamixel
    (XH430-W350-T) {value=6}

image of flipped dynamixel and stock kit

1.  Place the broad spacer washer into the dynamixel's drive-spline adjacent
    pocket: {value=7}

image of broad space washer

1.  Align the dot on the bearing output with the dot on the dynamixel output
    spline {value=8}

image of dots align

NOTE: Ensure it's properly aligned before applying any pressure. **No seriously,
go double check.**

1.  Gently press the bearing output down until the gap is closed between it and
    the dynamixel. If using an assembly press, do not force the assembly, apply
    smooth and firm pressure {value=9}

image of press

1.  Using the torque driver set to 0.6 Nm (60 cNm) with an M2 bit, install the
    1x M2.5x6 from the XH430-W350-T parts kit into the center of the output
    spline with the
    [Torque Dat tool](https://deepmind.onshape.com/documents/0ba344dda6e09547328e0696/v/92392d60ef98f2901f5156ce/e/58de78d6139db9c6235598f9).
    Set the motor aside for now. {value=10}

image of torque fastener

1.  Repeat step 1-10 to build the Head Yaw motor {value=11}

### Neck Pitch Motor Subassembly

neck pitch motor subassembly exploded view

#### Parts required

Prepare the following parts:

Qty | Part No.     | Description
--- | ------------ | ---------------------------------------------------------
1   | XH430-W350-T | Dynamixel
2   | N/A          | Spacers from XH430-W350-T parts kit
1   | EPX430-BR101 | Dynamixel enhanced output bearing
2   | N/A          | M2.5x17 SHCS with nylon patch from EPX430-BR101 parts kit
1   | N/A          | M2.5x8 SHCS with nylon patch from EPX430-BR101 parts kit
1   | HN12-I101    | Dynamixel idler horn kit
7   | 91263A421    | M2.5 X 5 SCREW FHCS
1   | 91458A116    | Threadlocker, Loctite 243
1   | N/A          | 3D Printed Neck Pitch Stop Upper
1   | N/A          | 3D Printed Neck Pitch Stop Lower
1   | 8613K11      | Neoprene foam sheet with adhesive backing

Prepare the following tools:

Qty | Tool                                  | Where used | Torque?
--- | ------------------------------------- | ---------- | -------
1   | xacto blade                           | Step 1     | N/A
1   | M1.5 Hex Driver bit                   | Step 13    | 0.6 Nm
1   | M2.0 Hex Driver bit                   | Step 7     | 0.6 Nm
1   | 10-80cNm Torque Driver                | Step 7     | 0.6 Nm
1   | Laser cut foam stencil for neck pitch | Step 1     | N/A

#### Instructions

WARNING: Avoid cuts, ensure your cut direction with a blade is away from your
digits and body.

1.  Prepare foam panel: Use scissors or laser cut stencils and a knife to cut
    out the
    [Foam Soft Stop Neck Pitch](https://deepmind.onshape.com/documents/0ba344dda6e09547328e0696/v/92392d60ef98f2901f5156ce/e/82d1fc98de6c8d07f2c26b93)
    panel. Set aside foam until the final step.

image of step 1's foam sheet cutout without stencil

1.  Remove the two dynamixel bolts adjacent to the output spline: {value=2}

image of two bolts that need to be removed

1.  Place 2x small spacers (from the XH430-W350-T parts kit) into the
    counterbored holes where the two bolts were removed from: {value=3}

image of image of two small spacers in place

1.  Place the broad spacer washer (from the EPX430-BR101 parts kit) into the
    dynamixel's drive-spline adjacent pocket: {value=4}

image of image of spacer washer

1.  Align the dot on the enhanced bearing output with the dot on the dynamixel
    output spline: {value=5}

image of spline dots aligned

NOTE: Ensure it's properly aligned before applying any pressure. **No seriously,
go double check.**

1.  Gently press the enhanced bearing output down until the gap is closed
    between it and the dynamixel. If using an assembly press, do not force the
    assembly, apply smooth and firm pressure. {value=6}
2.  Using the torque driver set to 0.6 Nm (60 cNm) with an M2 bit, install the
    1x M2.5x8 into the center of the output spline. Note that the motor
    backdriving torque sets the upper limit on screw installation torque and
    prevents damage to the motor.

image of bolts to be torqued for step 7

1.  Using the torque driver set to 0.6 Nm with an M2 bit, install the 2x M2.5x17
    SHCS (from the EPX430-BR101 kit) and the 2x M2.5x5 SHCS. {value=8}

image of bolts to be torqued for step 8

1.  Flip the dynamixel over, and remove the black plastic cover. {value=9}
2.  Press the plastic top hat bushing (from the HN12-I101 kit) into the
    dynamixel.
3.  Pop the silver idler horn (from the HN12-I101 kit) into the bushing. Note
    that it will click when fully seated.
4.  Pop the dust cover into place.

image of the complete dust cover + idler horn

1.  First, dab a small drop of Loctite 243 onto the 3x M2.5x5 FHCS. Using the
    torque driver set to 0.6 Nm with an M1.5 bit, install the 3x M2.5x5mm FHCS
    into the 3D Printed Neck Pitch Stop Upper. {value=13}

image of step 13's bolts to be torqued

1.  First, dab a small drop of Loctite 243 onto the 4x M2.5x5 FHCS. Using the
    torque driver set to 0.6 Nm with an M1.5 bit, install the 4x M2.5x5mm FHCS
    into the 3D Printed Neck Pitch Stop Lower. {value=14}

image of step 14's bolts to be torqued

1.  As a final step, remove the adhesive backing from the neck pitch foam you
    cut out during step 1. Install it into the pocket on the printed structure
    installed to the side of the subassembly in step 14. {value=15}

image of step 15's foam sheet installation location

### Neck Subassembly

neck subassembly exploded view 1 of 2
neck subassembly exploded view 2 of 2

NOTE: The above exploded views are missing the neck pitch motor. Refer to
detailed assembly pictures below.

#### Parts required

Prepare the following parts:

Qty | Part No.  | Description
--- | --------- | ------------------------------------
1   | N/A       | Neck Pitch Motor
1   | N/A       | Neck Pitch Motor Idler Shim
1   | N/A       | Neck Structure
8   | 90128A178 | M2x0.4 x 6mm SHCS
8   | 91263A411 | M2x0.4 x 4mm FHCS
1   | TO-5188L  | Torsion Spring
1   | N/A       | Spring Mandrel
1   | 91502A103 | M3x0.5 x 8mm SHCS
1   | N/A       | Dynamixel with idler horn installed
8   | 96817A317 | M2.5x 0.45 x 5mm SHCS
1   | 91458A116 | Threadlocker, Loctite 243
1   | N/A       | Dynamixel Motor Cable (Stock; 185mm)
2   | N/A       | Dynamixel Motor Cable (225mm)

Prepare the following tools:

Qty | Tool                   | Where used    | Torque?
--- | ---------------------- | ------------- | -------
1   | Tweezers               | Step 1        | N/A
1   | 10-80cNm Torque Driver | Step 5,6,9,10 | 30 cNm
1   | M1.5 Hex Driver bit    | Step 5,6      | 30 cNm
1   | Needle Nosed pliers    | Step 7        | N/A
1   | M2.5 Hex Driver bit    | Step 9        | 30 cNm
1   | M2.0 Hex Driver bit    | Step 10       | 30 cNm

#### Instructions

1.  Insert the neck pitch motor into the neck structure first, then insert the
    idler shim between the motor and the structure. {value=1}

image of step 1's inserting shim between neck pitch motor and idler shim

1.  Confirm alignment of the shim holes with the fastener holes on the motor.
    {value=2}

image of step 2's aligning shim holes

1.  Turning the motor over to the output side, rotate the neck structure to
    align the arrow with the marked dot on the motor. {value=3}

image of step 3's arrow to marked dot alignment

1.  Turn the motor back to the idler horn side to bias the neck structure
    towards the idle side. Torque down the 8x M2x4mm FHCS to 30 cNm. Torque down
    in a star pattern. {value=4}

image of step 4's torque M2x4 FHCS

1.  Turn the structure over one more time and torque down the 8x M2x6mm SHCS to
    30cNm. Set aside for now. {value=5}

image of step 5's torque M2x6 SHCS

1.  With pliers, bend the torsion spring to the correct configuration. This is
    estimated by the
    [drawing of TO-5188L](https://deepmind.onshape.com/documents/0ba344dda6e09547328e0696/v/92392d60ef98f2901f5156ce/e/19f8cd6aba48b1b9441f32f9)
    , however for a one-off build, the following ad hoc procedure may provide
    better results: (a) Place the spring into the mandrel. (b) Mark the location
    of the first bend with a permanent marker. (c) Make a bend using two pairs
    of pliers (regular + needle nose work well), accounting for the bend radius.
    (d) Put the spring back in the mandrel, check against the part, and repeat
    from (b) to make more bends. (e) Test the spring by running the neck through
    its full range of motion. Make any needed adjustments. {value=6}

image of step 6's bent torsion spring

1.  Install the torsion spring, using pliers to bend the spring into the
    position of the neck structure. {value=7}

image of step 7's overall spring placement
image of step 7's bend in spring positioning

1.  Install the spring mandrel on top of the spring and torque down the M3x8mm
    SHCS to 30cNm. {value=8}

image of step 8's mandrel fastened on

1.  Insert the head yaw motor (dynamixel with idler horn installed) and torque
    down the 8x M2.5x5mm to 30cNm. These screws (and other motor mount
    locations) are critical and loosening due to vibration should be prevented
    using Loctite 425 (cyanoacrylate based) to avoid interaction between the
    loctite and plastic parts. {value=9}

image of step 9's sides of head yaw motor
image of step 9's bottom of head yaw motor

1.  Install the stock 185mm Dynamixel motor cable on neck pitch motor. {value=10}

    NOTE: The original CAD indicates the spring is blocking the port. Depending
    on how the spring is bent, there may be a need to undo the spring to install
    the cable.

image of step 10's cable insertion to neck pitch motor under spring

1.  Install one of the custom 225mm Dynamixel motor cable on other port of the
    neck pitch motor. Plug the cable to the motor before dropping the motor into
    the clevis of the neck structure. {value=11}

image of step 11's other cable insertion to neck pitch motor

1.  With the same motor cable in step 11, wrap the cable around the mandrel of
    the neck structure and connect the other end of the cable to the head yaw
    motor. {value=12}

    NOTE: When wrapping the cable, the cabled should go over and under the
    mandrel. The numbers in the image indicate the order.

image of step 12's cable winding around mandrel
image of step 12's cable insertion to head yaw motor from neck pitch motor

1.  Install the other custom 225mm Dynamixel motor cable on the other port of
    the head yaw motor. Then, test the full range of motion for the cable
    service loop before proceeding. {value=13}

image of step 13's other cable insertion to head yaw motor

### Head Subassembly

Left of head subassembly exploded view

Right of head subassembly exploded view

#### Parts required

Prepare the following parts:

Qty | Part No.  | Description
--- | --------- | -----------------------------------------
1   | N/A       | Head structure
1   | N/A       | Jaw Motor
6   | 91290A106 | SHCS M2.5x16
1   | 9714K18   | Wave, 0.787" ID, 1.094" OD, 0.012" Thick
1   | 90214A441 | Shim, 0.5mm Thick, 20mm ID
1   | N/A       | Space Washer, printed
8   | 90128A177 | SHCS M2x5
8   | 90128A179 | SHCS M2x8
8   | 98688A110 | Small OD flat washer, 2.2mm ID, 4.5mm OD
1   | N/A       | Upper Jaw Template
1   | 8613K11   | Neoprene foam sheet with adhesive backing
1   | N/A       | Jaw Upper Structure
4   | 91502A103 | SHCS M3x8
1   | 91458A116 | Threadlocker, Loctite 243
1   | TY23MX    | Zip tie 92mmx2.3mm

Prepare the following tools:

Qty | Tool                   | Where used       | Torque?
--- | ---------------------- | ---------------- | -------
1   | M2.0 Hex Driver Bit    | Step 2, 4, 5, 7  | 0.3 Nm
1   | Torque Dat tool        | Step 5, 7        | N/A
1   | M1.5 Hex Driver Bit    | Step 9, 10       | 0.3 Nm
1   | M2.5 Hex Driver bit    | Step 12          | N/A
1   | 10-80cNm Torque Driver | Step 4, 7, 9, 10 | 0.6 Nm
1   | Xacto blade            | Step 11          | N/A

#### Instructions

WARNING: Avoid cuts, ensure your cut direction with the blade is away from your
digits and body.

1.  Ensure head structure has 9x M3 heat inserts. If not, refer to the Head
    Structure section.

1.  Remove 3 out of 4 of the fasteners on each side of the Jaw motor that will
    be fasten to the head structure with a M2 Hex bit

image of remove 3 screws on each side

1.  Pass the built 225mm motor cable that is connected to the head yaw motor
    through the window that's on the side through the right side (refer to image
    for direction) of the head structure. Connect the cable end to the jaw motor
    port. {value=3}

image of cable passthrough
image of cable passthrough

1.  Using the torque driver set to 0.3 Nm (30 cNm) with a M2 Hex bit, install
    the 3x SHCS M2.5x16 on **each** side of the dynamixel. The yellow shim
    pictured in the photo should not be needed for a well-toleranced print.
    These fasteners on motor mount locations are critical and loosening due to
    vibration should be prevented using Loctite 425. {value=4}

image of fasten

1.  With an M2 Hex bit, undo the fastener from the center of the output spline
    with the Torque Dat tool. Set the fastener aside for now. {value=5}

image of undo fastener

1.  Add wave(PN 9714k18) - shim(PN 90214A441) stack to the output side of the
    head yaw motor with the shim flushed on the motor and the wave on top
    between the shim and the head structure. Align the motor into the Head
    Structure {value=6}

image of wave shim stack

NOTE: This next step may need one person to push the motor towards the output
side and another person insert the space washer on the idle side

1.  Insert the printed space washer to the idle side. Using the torque driver
    set to 0.6 Nm (60 cNm) with an M2 Hex bit, refasten the fastener to the
    center of the output spline with the Torque Dat tool {value=7}

image of space washer

1.  Align the motor output marker dot to the arrow on the head structure. Flip
    the head structure over to see the arrow {value=8}

image of arrow and dot

1.  Fasten the head structure to the motor with 8x SHCS M2x5 on the output side
    with a M1.5 hex bit using the torque driver set to 0.3 Nm (30 cNm). Threaded
    holes on the motor are very shallow, <2mm depth. Take care to ensure that
    the screws do not bottom out on the motor body. {value=9}

image of output side

1.  Fasten 8x SHCS M2x8 along with 8x small OD flat washer (PN 98688a110) for
    the idle side using the torque driver set to 0.3 Nm (30 cNm) {value=10}

image of idle side

1.  Using the upper jaw template, cut the foam and install onto the Jaw Upper
    Structure {value=11}

image of upper jaw

1.  Secure the part to the Head Structure using 4x SHCS M3x8 with a M2.5 bit
    {value=12}

image of upper jaw attachment

1.  Loosely zip tie the motor cable to the outer anchor point on the head
    structure. {value=13}

image of ziptie anchor to head structure

### Camera Subassembly

Camera subassembly exploded view

NOTE: The above exploded view is showing 4 screws to mount the OAK module onto
the 3D printed camera bracket, however only 3 screws will fit.

#### Parts required.

Prepare the following parts:

Qty | Part No.           | Description
--- | ------------------ | -------------------------
2   | OAK-FFC-OV9782-M12 | Luxonis cameras
2   | LN056              | OAK lens
4   | 2000035198         | Lens lockrings
1   | A00470             | OAK-FFC-4P module
1   | N/A                | 3D printed camera bracket
1   | N/A                | USB-C to USB-C cable
8   | 96817A312          | TF M2x6
3   | 96817A317          | M2.5x6
3   | 91502A103          | SHCS M3x8
2   | N/A                | FFC Ribbon

Prepare the following tools:

Qty | Tool                   | Where used     | Torque?
--- | ---------------------- | -------------- | -------
1   | Spudger                | Step 1, 13, 16 | N/A
1   | T6 Driver bit          | Step 5         | 0.6 Nm
1   | T8 Driver bit          | Step 14        | N/A
1   | 10-80cNm Torque Driver | Step 15        | 0.3 Nm
1   | 1.85 mm drill bit      | Step 1         | N/A
1   | 2.3 mm drill bit       | Step 2         | N/A

#### Instructions

1.  If needed, carefully chase 8x holes for the camera mount with a 1.85 mm
    drill bit or reamer. Do not tap these holes, as they will subsequently take
    thread-forming screws.

image of the eight holes to chase for M2

1.  If needed, carefully chase 3x holes for the OAK Module with a 2.3 mm drill
    bit or reamer. Do not tap these holes, as they will subsequently take
    thread-forming screws. {value=2}

image of the three holes to chase for M2.5

1.  Remove the FFC from the PCBA. {value=3}

image of how to remove the ribbon cable

1.  Align the camera PCBA over bracket holes. {value=4}
1.  Using the hand driver with an T6 bit, install the 4x TF M2x6(96817A312) in
    the following cross pattern. Install all 4 screws half way in before hand
    torquing it all down.

image of the pattern for the screws

1.  Remove the lens by holding the camera fixture firmly and slowly twist the
    lens counterclockwise. {value=6}

WARNING: IT IS NOT POSSIBLE TO CLEAN SENSOR. PREVENT DIRT AND DUST FROM GOING IN
BY MINIMIZING THE AMOUNT OF TIME THE SENSOR IS UNCOVERED

1.  Grab a lockring and twist it onto the Low Distortion M12 lens. {value=7}

image of lockring on the M12 lens

1.  Install the Low Distortion M12 lens by holding the camera fixture firmly and
    slowly twist the lens clockwise until the lens are half way in. {value=8}

image of M12 lens halfway in

WARNING: DO NOT TIGHTEN THE LENS ALL THE WAY, LEAVE IT HALFWAY TO ADJUST THE
FOCUSING IN A LATER STEP

1.  Re-attach the FFC that was disconnected from the first step. {value=9}
1.  Repeat the same process on the other side. {value=10}

image of both side cameras install

1.  Using a hand driver with T8 bit, install 1x M2.5x6(96817A317) onto the
    bottom right of the camera bracket halfway in. {value=11}

image of where to install the first screw

1.  Route the right camera’s FFC ribbon in the camera bracket as shown.
    {value=12}

image of how to route the right FFC cable

1.  Remove the OAK-FFC-4P from its packaging and locate the CAMB-2L in the back.
    Handle with care to prevent damage to the board with any built-up
    electrostatic charge. A wrist strap for grounding is a good idea. {value=13}

image of where the CABM-2L is located

1.  Attach the right camera’s FFC into the CAMB-2L, oriented so that the wider
    trace on the FFC is to the side of the connector labeled "26". {value=14}

image of how the FFC should be plugged in

1.  Using a hand driver with T8 bit, install 2x M2.5x6(96817A317) on the top
    right and bottom left to loosely secure the OAK-FFC-4P onto the camera
    bracket. {value=15}
1.  Using a torque driver set to 0.3Nm (30 cNm) with an T8 bit, torque all 3x
    M2.5x6(96817A317). {value=16}

image of the pattern for the screws

1.  Route the left camera’s FFC ribbon cable into the CAMA-4L, which is parallel
    CAMB-2L. You may have to make a couple sharp bends on the cable--but try to
    avoid unnecessary extra sharp bends. {value=17}

image of how to route the left FFC cable

1.  Pre-plug the USB-C cable. {value=18}

image of how USB-C installed

1.  Using a torque driver set to 0.3Nm (30 cNm) with an M2.5 hex bit, install
    SHCS M3x8(91502A103) to mount the camera subassembly to the head structure.
    As the positional stability of the cameras is critical, use Loctite 425 on
    these fasteners. {value=19}

Image of the completed physical subassembly

NOTE: Physical camera subassembly completed. Continue to Camera Focusing section
to have a functional camera subassembly.

### Lower Jaw Subassembly

lower jaw subassembly exploded view

NOTE: Exploded view does not include Jaw motor. Refer to detailed assembly
pictures below.

#### Parts required

Prepare the following parts:

Qty | Part No.  | Description
--- | --------- | -----------------------------------------
1   | N/A       | Lower Jaw Structure
1   | 8613K11   | Neoprene foam sheet with adhesive backing
1   | N/A       | Lower Jaw shell
1   | 91502A103 | M3x0.5 x 8mm SHCS
12  | 90128A178 | M2x0.4 x 6mm SHCS

Prepare the following tools:

Qty | Tool                                 | Where used | Torque?
--- | ------------------------------------ | ---------- | -------
1   | xacto blade or scissors              | Step 1     | N/A
1   | Laser cut foam stencil for lower jaw | Step 1     | N/A
1   | M2.5 Hex Driver bit                  | Step 3     | 30 cNm
1   | M1.5 Hex Driver bit                  | Step 6     | 30 cNm
1   | 10-80cNm Torque Driver               | Step 3,6   | 30 cNm

#### Instructions

WARNING: Avoid cuts, ensure your cut direction with the blade is away from your
digits and body.

1.  Prepare foam panel: Use scissors or laser cut stencils and a knife to cut
    out the
    [Foam Soft Stop lower jaw](https://deepmind.onshape.com/documents/0ba344dda6e09547328e0696/v/92392d60ef98f2901f5156ce/e/b567c901a6f57977d77b8571)
    panel. {value=1}

image of step 1's foam sheet cutout without stencil

1.  Remove the adhesive backing and firmly apply the foam to the inner curvature
    of the lower jaw structure. {value=2}

image of step 2 foam on jaw structure

1.  Flip the structure over to the bottom and align the lower jaw shell with the
    structure. Torque down the fasteners using M3x8mm to 30 cNm. {value=3}

image of step 3 shell attached

1.  Attach the lower jaw to the jaw motor. The alignment is determined by an
    arrow that points away from the dot on the output side of the jaw motor.
    {value=4}

image of step 4 lower jaw alignment

1.  Torque down both sides of the jaw structure with 12x M2x6mm to 30 cNm.
    {value=5}

image of step 5 output side fastened

### Final Integration

#### Parts required

Prepare the following parts:

Qty | Part No.     | Description
--- | ------------ | ---------------------------
4   | 340-M2512-61 | M2.5X12
3   | 91502A103    | M3x0.5 x 8mm SHCS
6   | 91263A823    | M3x0.5 x 8mm FHCS
3   | 90128A216    | M4x0.7 x 20mm SHCS
4   | 91100A110    | washer 2.7ID
1   | N/A          | 3D printed neck shell
1   | N/A          | 3D printed neck shell cover
1   | N/A          | Jackson PCBA
1   | N/A          | Fei-Fei power cable.

Prepare the following tools:

Qty | Tool                   | Where used  | Torque?
--- | ---------------------- | ----------- | -----------------
1   | 10-80cNm Torque Driver | Step 10, 17 | 0.3 Nm and 0.4 Nm
1   | Small torque wrench    | Step 4      | 0.5 Nm
1   | 2mm HEX T-handle       | Step 3      | N/A
1   | 3mm HEX T-handle       | Step 5      | N/A
1   | 3mm Low profile L-key  | Step 6      | N/A
1   | M2.5 Hex bit           | Step 10     | 0.4 Nm
1   | M2 Hex bit             | Step 17     | 0.3 Nm

#### Instructions

1.  Remove the Deep Fry Basket (DFB) from the Barkour Robot. {value=1}
1.  Pre-install the 4x m2.5X12(340-M2512-61) with washer 2.7ID(91100A110) into
    the holes of the 3D printed neck shell. {value=2}

image of pre-installed screws

1.  Using a 2mm HEX T-handle, install 4x M2.5X12(340-M2512-61) to mount the 3D
    printed neck shell onto the neck pitch motor. {value=3}

image of mounting the 3D printed shell

1.  Using a small torque wrench set to 0.5Nm(50 cNm) with 2mm HEX BIT, torque
    the screws down in the following cross pattern. {value=4}

image of cross pattern

1.  Using a 3mm HEX T-handle, install 1x M4x0.7(90128A216) to mount the other
    end of the 3D printed neck shell onto the torso. {value=5}

image of mounting the neck shell onto the torso

1.  Using a low profile 3mm l-key to install the other 2x M4x0.7(90128A216)
    until its hand tight. {value=6}
1.  Route the USB-C from the OAK module into the left hole of the neck shell.
    {value=7}

image of the USB-C route

1.  Route the motor cable to the right hole of the neck shell. {value=8}

image of the motor cable route

1.  Plug the power cable into the Fei-Fei board located inside the torso and
    route the other end into the neck base. {value=9}

image of power cable from Fei-Fei board

1.  Using the torque driver set to 0.4 Nm (40 cNm) with an M2.5 hex bit, install
    3x M3x0.5 x 8mm SHCS(91502A103) to mount the Jackson PCBA onto the neck
    shell cover. {value=10}

image of Jackson board mounted

1.  Plug in the motor cable into the Jackson board. {value=11}

image of where to plug in motor cable

1.  Plug in the USB-C from the OAK module into the Jackson board. {value=12}

image of where to plug in USB-C

1.  Plug in the power cable into the Jackson board. {value=13}

image of where to plug in power cable

1.  Route the USB-C from the NUC through DFB like shown and through the neck
    base. {value=14}

image of where to route the USB-C from NUC

1.  Plug in the USB-C from the NUC into the Jackson board. {value=15}

image of where the USB-C cable from NUC go

1.  Install the DFB back into the robot. {value=16}

WARNING: Be careful not to crush any cables. Double check the power cable that's
plugged into FEI FEI and the USB-C from NUC to ensure that there isn’t too much
tension.

1.  Using the torque driver set to 0.3 Nm (30 cNm) with an M2 bit, install 6x
    M3x0.5 x 8mm FHCS(91263A823) to mount the neck base cover. {value=17}

image of cross pattern

### Cosmetic Shell Subassembly

shell subassembly exploded view

#### Parts required

Prepare the following parts:

Qty | Part No.  | Description
--- | --------- | -----------------
11  | 91502A103 | M3x0.5 x 8mm SHCS

Prepare the following tools:

Qty | Tool                | Where used | Torque?
--- | ------------------- | ---------- | -------
1   | M2.5 Hex Driver bit | Step 3     | 30 cNm

#### Instructions

1.  The head shell must be applied first. Tilting the head forward to get the
    lens holes to align first makes this step a little easier. Carefully guide
    the head shell on top of the head structure. Make sure to monitor the lens
    during application to avoid scratching the lens. The head shell should rest
    on the head structure ends. {value=1}

image of step 1 structure to head shell mounting point

1.  Torque down 2x M3x8mm on each side of the head, below the ear, to 30 cNm.
    {value=2}

image of step 2 fastener position head shell left side

1.  In the upper jaw, torque down 2x M3x8mm to 30 cNm. {value=3}

image of step 3 fastener positions upper jaw

1.  With the left neck shell, torque down 2x M3x8mm on the neck structure to 30
    cNm. {value=4}

image of step 4 fastener positions left neck shell

1.  With the right neck shell, torque down the remaining 5x M2x8mm on the neck
    structure and opposite shell to 30 cNm. {value=5}

image of step 5 fastener positions right neck shell

1.  Complete a final assembly check. Check range of motion for each joint
    individually, then compounded motions. Address any areas where cables add
    significant load to the motors. Check for counter-balance spring behavior.
    Then power the motors and run each motor to ensure the software-configured
    limits (motor parameters and virtual hard-stop) are correct.

## Camera Focusing

### Prerequisites

*   git
*   a USB port
*   basic command line knowledge

### Setup and focusing

1.  Install the Luxonis' depthai-python repo according to the
    [Luxonis instructions](https://docs.luxonis.com/projects/api/en/latest/install/).
2.  Plug the USB cable from the actuated head assembly into your computer.
3.  Run the script at `depthai-python/examples/ColorCamera/rgb_video.py` to open
    a viewer window and see the output from the camera. If your camera has been
    connected to the `CAM_B` port, you may need to open the script in a text
    editor of your choice and replace references to `CAM_A` with `CAM_B`.

```
cd depthai-python/examples/ColorCamera
python3 rgb_video.py
```

1.  Aim the head where it can see far from your desk. {value=4}
2.  Slowly adjust the lens until objects very far away are in focus.
3.  Aim the head to where it can see objects ~20-30cm away.
4.  Slowly tune the lens focus until those objects are reasonably well focused.
5.  Hold the lens in place, and gently tighten the lockring until tight.
6.  Verify focus by aiming the head further away. Repeat prior steps if needed.

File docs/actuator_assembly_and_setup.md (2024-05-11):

# Single Actuator Assembly and Software Configuration

[TOC]

## Overview

The following document details how to build a single motor sub-assembly and
configure it.
Preview Sub-assembly

Three "monomotors" form a trimotor, and four trimotors complete a single robot.

Note: This document describes the single actuator assembly using the
Ada/Gebru/Cortes motor driver PCBAs. The Holberton PCBA incorporates all
features of the Ada, Gebru & Cortes boards into a single PCBA and can be used as
a drop-in replacement.

## Parts Needed

| Part Name | Quantity | Description & Details |
| --- | :---: | --- |
| ADA PBCA | 1 | Motor encoder and monitors |
:                             :             : temperature.                    :
| Thermistor                  | 1           | Attached to the ADA.            |
| ADA Separator               | 1           |                                 |
| Ak80-9 motor                | 1           |                                 |
| M2x8mm SHCS, BO             | 3           | Fastens ADA & intermediary ADA  |
:                             :             : separator piece into the motor. :
| Heatsink                    | 1           | Machined part                   |
| M3x5mm SHCS, BO             | 8           | Fastens motor to heatsink.      |
| Thermal Pads                | *as needed* | *Advised to pre-cut prior to    |
:                             :             : assembly*                       :
| Gebru PCBA                  | 1           |                                 |
| Cortes PCBA                 | 1           |                                 |
| Board motor screw terminals | 3           | Connects motor phase-leads to   |
:                             :             : the PCBA cluster.               :
| Male XT30 pigtail           | 1           | Power connector on the Gebru.   |
| Encoder (ADA) harness       | 1           | Connects Gebru and ADA.         |
| M3x12mm Philips (nylon)     | 3           | Keeps the boards and motor      |
:                             :             : together.                       :
| M3x6mm SHCS (nylon)         | 1           | Same as above.                  |

## Assembly Procedure

1.  Prepare the ADA board.

    A. Solder the thermistor onto the PCBA at the two leads.

    thermistor

    B. Laser cut an Ada separator

    ADA separator

2.  Install the ADA on the AK80-9 motor as shown below.

    A. Starting with a fresh motor, remove the stock cover to expose leads.

    Ak80-9

    Motor cover

    B. Place the separator piece on the exposed motor...

    Motor with Separator

    C. ...and fasten the board in-place to hand-tightness with the x3 M2x8mm
    bolts.

    Install assembly

3.  Install the heatsink onto the motor assembly.

    A. Stage the heatsink on the motor as shown below.

    NOTE: Make sure the phase leads are routed under the bridge on the heatsink
    and **not crossed over each other**. *Also recommended to bend the
    thermistor as shown so it’s pointing upward and doesn't get pinched.*

    Staging Heatsink

    B. Apply Loctite 243 (*blue*) and install screws. Torque down in a star
    pattern to 2Nm.

    C. Glue the thermistor down into the notch on the heatsink.

    Glue thermistor

    D. Cut out a ~10x35mm patch of thermal pad and stick it onto the bridge.

    Thermal pad

4.  Pair a Gebru PCBA with a Cortes PCBA to assemble our motor control cluster.

    A. Get a fresh Gebru board, three(3) board motor screw terminals, one (1)
    male XT30 pigtail, and one (1) encoder (Ada) harness.

    Gebru board

    B. Strip the encoder cable wires (28ga AWG) and xt30 pigtail (16ga AWG) to
    ~50-60mm, then solder them to the Gebru along with the 3 screw-in terminals
    for the phase leads.

    Encoder cables

    Encoder cables

    Encoder cables

    Encoder cables

    C. Get a prepped Gebru, one (1) fresh Cortes, three (3) 4mm nylon spacers,
    three (3) M3x10mm nylon screws, and one(1) M3x6mm nylon screw.

    Motor and Gebru

    E. **CAREFULLY** marry the Gebru and Cortes together with the pin headers.
    **It is very easy to break or bend these header pins.**

    Gebru & Cortes

    F. Make sure the x3 nylon spacers are in the corresponding positions. These
    line up to form the mounting points for the boards and the motor assembly.

    Gebru & Cortes 2

5.  Installing the PCBA cluster onto the motor sub-assembly.

    A. Place the married Gebru and Cortes onto a prepped motor as shown below.
    Make sure to route the phase leads through the center hole of the board
    (**do not** cross the phase leads).

    Gebru/Cortes/motor

    B. Secure through the Cortes & Gebru into the motor with x3 M3x12mm nylon
    Philips head screws. In the *remaining hole only on the Gebru*, next to the
    red caps, use the shorter x1 M3x6mm nylon bolt to secure.

    C. Plug in the encoder cable into the ADA.

    ADA Plugged In

    D. Lastly, attach the phase leads to the screw-in terminals on the Gebru
    board(***Remember to not cross the phase leads and take caution not to short
    against the capacitors!***).

    Phase Leads vs Capacitor Precaution

NOTE: You now have a complete motor assembly that's ready for flashing.
Complete assembly

## Flashing and Calibration Instructions

After assembling the motor, we have to ensure that all the electronic components
are stable, the proper firmware is installed on our boards, and the motor moves
as expected.

### Required Equipment

| Part Name | Quantity | Description & Details |
| --- | :---: | --- |
| Mataric board | 1 | Provides debug buttons and LEDS  |
:                                :          : for motor driver.                :
| J-Link Pro                     | 1        | Programmer, includes FC-20P      |
:                                :          : cable.                           :
| USB A-B cable                  | 1        | Connects J-Link to computer for  |
:                                :          : programming.                     :
| USB A to micro USB             | 1        | Connects Mataric to computer for |
:                                :          : debug logs.                      :
| Samtec 20 pos cable            | 1        | Connects Mataric and Cortes.     |
| USB → Ethernet dongle (TP-Link | 1        | Connects computer to EtherCAT on |
: UE306)                         :          : Cortes.                          :
| Ethernet -> EtherCAT connector | 1        | Connects dongle to Cortes.       |
| PSU -> STO/EtherCAT connector  | 1        | Enables STO (ECAT1) on Cortes.   |
| XT30 female -> PSU             | 1        | Powers the motor.                |
| USB extension cable (optional) | 1        | Dongle is short. Maybe need      |
:                                :          : extension to reach the computer. :
| Power Supply Unit (PSU, 2      | 1        | Powers motor setup and enables   |
: channels)                      :          : STO.                             :

Programming Parts

Motor Setup Parts

### Hardware Setup

1.  Assemble the programming components.

    A. Connect the J-Link to the computer with the USB A-B cable.

    B. Connect the J-Link to the Mataric with the FC-20P cable that comes with
    the J-Link.

    C. Connect the Mataric and Cortes with the Samtec 20 pos cable.

    D. Connect the Mataric to the computer with the USB A to micro USB cable.

2.  Plug the EtherCAT and power connectors into the Cortes board:

    A. First, verify that all power supplies to be used are working and won't
    blow up the boards. To do this, turn them on while disconnected and ensure
    they're set to the desired voltage/current settings.

    NOTE: STO power supply is typically set to **24.0V** (*current turned all
    the way down*) and the main supply is set to **48.0V / 300mA** initially.

    B. Connect the XT30 female -> PSU to a 48-60V power supply terminal and then
    to the XT30 male power connector attached to the Gebru board of the motor
    assembly.

    C. Similarly, connect the PSU → STO/EtherCAT connector first to the
    unpowered 20-24V power supply terminals and then to the "ECAT1(OUT)"
    connector on the Cortes board.

    D. Next, connect the USB → Ethernet dongle (TP-Link UE306) to the computer.
    A USB extension cable may be needed. Connect this dongle to the Ethernet →
    EtherCAT cable, and connect the nanofit end of this cable to the "ECAT0(IN)"
    connector on the Cortes board. All connectors should now be plugged in.

3.  Test the motor assembly before you begin flashing by turning on both power
    supplies at limited power outputs:

    A. Set the STO power supply to ~24.0V and start with the current set to 0A.
    Slowly increase the fine current setting until the monitored current reaches
    ~7mA.

    NOTE: If the current never reaches this value, or if it increases to greater
    than 14mA, turn off the power, and disconnect the board from all cables.
    This board is likely damaged and will need debugging.

    B. Next, test the main power on the board. Set it to 48.0V / 300mA and turn
    it on. You should see the lights on the board start to light up and it
    should draw ~200mA. This amount of current/power will not be exact. If the
    assembly is not drawing the max current (300mA), increase the current limit
    to something > 10A. Watch/listen/smell for sparks and/or damaged components
    during this whole process.

    If anything goes wrong, turn off the power, and disconnect the board from
    all cables. This motor assembly is damaged and will need repair. Otherwise,
    this motor is ready for flashing.

### Software Setup

See [ethercat config](ethercat_config.md), [firmware](firmware.md), and
[motor control](motor_control.md) docs for details.

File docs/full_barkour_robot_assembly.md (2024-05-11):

# Full Barkour Robot Assembly

[TOC]

This page describes how to assemble a complete Barkour Robot. ***It assumes that
all relevant preparation steps and sub-assemblies have been completed.***

The guides for the sub-assemblies can be found at these locations:

*   [Actuator assembly and setup](actuator_assembly_and_setup.md)
*   [Hip cover assembly](hipcover_assembly_instructions.md)
*   [Leg linkage assembly](leglinkage_assembly_instructions.md)
*   [Wireless E-stop (STO) assembly](wsto_assembly.md)
*   [IMU configuration](imu_config.md)

Note: If you'd like to build the actuated head variant, first assemble a robot
with a static head (this doc), then follow the
[actuated head assembly](actuated_head_assembly.md) instructions.

## Overview

NOTE: In an attempt to optimize the flow of building the robot and minimize
potential pain-points, we've devised these distinct phases in a recommended
sequence diagram.

general order of operation

1.  **Deep Fry Basket**

    *   In this stage we're bringing together all unique and associated assets
        of a Barkour Robot's electronics basket such as its central compute and
        sensor systems.
    *   Once designated, every part in this assembly should stay together, even
        when displaced into a different robot assembly.
    *   This module does not get its final configuration until the end, due to
        how the camera is mounted via special structure attached to the torso.

2.  **Torso**

    *   This is the "body" upon which four "legs" and "brain" can be grafted.

3.  **Trimotor Assembly**

    *   Three mono-motor sub-assemblies come together to form a specific leg.
    *   There are only FOUR valid configurations:
        *   **FL** \(**F**ront **L**eft\)
        *   **HL** \(**H**ind **L**eft\)
        *   **FR** \(**F**ront **R**ight\)
        *   **HR** \(**H**ind **R**ight\)
    *   The specific hip bracket dictates the **R**ight or **L**eft nature.
    *   And the specific cable harness designates the additional **F**ront or
        **H**ind orientation.

4.  **Torso Assembly**

    *   At this phase we have a completed torso with partially finished "legs".
    *   All "legs" currently terminate at the "knee" actuator and do not have
        shells or proper feet yet.
    *   One of each orientation trimotors is installed and wired in the
        appropriate sequence.
    *   The ECAT chain ordering is further elaborated in the
        [Range of Motions doc](barkour_rom.md).

5.  **"Leggy"**

    *   We attach the rest of the leg linkages and shells to the torso assembly.
    *   This is complete *from a mechanical perspective.*

6.  **Barkour Robot \[COMPLETE\]**

    *   The robot has a complete body with fully-assembled legs.
    *   The "brain" is all wired up and assets are all in their finalized spots.
    *   The assembled robot is ready for software bringup and general use.

## Individual Modules

NOTE: The following three modules are not dependent upon one another and
therefore can be built in-parallel.

### Deep Fry Basket (DFB)

The DFB goes through TWO DISTINCT PHASES during assembly:

*   **PHASE 1** - "Universal"

    *   Mechanically and electrically indistinguishable from one another.
    *   Can be swapped around with minimum fuss.

*   **PHASE 2** - "Designated"

    *   Assigned a specific NUC computer and its associated subcomponents.
    *   These items are explicitly paired with the NUC via software configs.

#### Parts Needed for PHASE 1: "Universal DFB"

| Part Name | Quantity | Description & Details |
| --- | :---: | --- |
| 3D-printed Deep Fry Basket | 1 | |
| RUS_Power_In | 1 | Red and black cable bundle with |
:                            :          : anode and cathode electrodes         :
:                            :          : soldered in a specific orientation   :
| U-shaped Electrode         | 1        | Additional power leads               |
| Battery Holder             | 1        | Part that sandwiches the             |
:                            :          : afforementioned leads in-place with  :
:                            :          : the + and - signs                    :
| M3x8mm SHCS                | 2        | Screw that secures the Battery       |
:                            :          : Holder to the DFB                    :
| RGB Fan                    | 2        | Modified with 2POS nanofit molex     |
:                            :          : connectors                           :
| M3x18mm SHCS               | 4        | Secures fans into the DFB            |
| M3 Nuts                    | 4        |                                      |
| Power_Switch               | 1        |                                      |
| E-stop Antenna             | 1        |                                      |
| Antenna Panel              | 1        |                                      |
| M3x6mm SHCS                | 2        |                                      |
| Rus PCBA                   | 1        | Power distribution board             |
| M3x12mm CSS                | 2        |                                      |
| M3x16mm CSS                | 1        | We need a longer countersunk bolt to |
:                            :          : hold the Rus in-place                :

1.  Install the electrodes.

    A. The black lead is longer than the red one; *you can’t get this wrong
    unless it was soldered incorrectly.*

    Rus PWR In cable and Metal U-Tab

    B. Pressed into the DFB slots in the shown order.

    DFB PWR Metal Prongs In-place

    C. Hand-tighten the Battery Holder with the x2 M3x8mm bolts.

    Battery Holder Over Power Leads

2.  Install the NUC-cooling fans into the shell.

    A. Each is secured via x2 M3x18mm bolts and nuts. Oriented so they shoot air
    ***upwards and away*** from the robot torso.

    Fan 1

    Fan 2

    B. Molex connectors funneled to robot back side right (*it will plug into
    the RUS when it gets there*).

    Fan 3

    Fan 4

3.  Install the power button. Confirm the o-ring is present, and then tighten
    the retention nut to feel with pliers.

    Installed Power Button

4.  Install the cover with the on-robot E-stop antenna.

    A. Take care not to damage the delicate cable. Route it to the left side
    (*it will plug into the Hopper when it shows up*).

    STO Antenna

    B. Hand-tighten with x2 M3x6mm bolts to the top.

    Antenna Cover Installed

5.  Install the RUS power distribution board.

    A. The board mounts to the right side of the DFB with x2 M3x12mm (shorter)
    and a single M3x16 through the center. *We can leave the fourth spot open
    for now and zip-tie it down later.*

    Rus Fastened to DFB

    B. Top-side ports should align like so:

    Rus Topside Ports

    C. Connect FANS from step #2 into J8 and J9. Then plug in the electrode
    leads from step #1 into the appropriate slot.

    Fans Plugged into Rus

    Electrode Plugged into Rus

NOTE: Up to this stage, the assembly is a “universal DFB”. But after this phase
this DFB is associated with a specific NUC compute and its associated parts.

#### Parts Needed for PHASE 2: "Designated DFB"

| Part Name | Quantity | Description & Details |
| --- | :---: | --- |
| Deep Fry Basket | 1 | This is what we built up in PHASE 1 |
| Hamilton with IMU | 1 | Measures IMU data |
: Assembly                  :          :                                       :
| M2x16mm SHCS              | 3        | Keeps the IMU secured to the bottom   |
:                           :          : of the DFB                            :
| M2 Locknuts               | 3        |                                       |
| NUC                       | 1        | CENTRAL COMPUTING UNIT FOR THE ROBOT  |
:                           :          : DOGGY                                 :
| Rus_to_NUC                | 1        | Power cable for the NUC               |
| M3x6mm SHCS               | 4        | Secures NUC to the backside of the    |
:                           :          : DFB                                   :
| Hopper PCBA & XBee        | 1        | Remote E-stop mechanism               |
: Transceiver               :          :                                       :
| M3x6mm SHCS               | 4        | Four bolts for securing the Hopper to |
:                           :          : the DFB                               :
| Rus_to_Hopper             | 1        | Cable                                 |
| USB to Ethernet Adaptor   | 1        |                                       |
| NUC_ECAT_DFB              | 1        | Cable                                 |
| USB Panel                 | 1        | 3D-printed part to mount the panel    |
:                           :          : mount cables three USB-C slots        :
| PanelMount_USB_A_to_C     | 1        | Cable                                 |
| PanelMount_USB_C_to_C     | 1        | Cable                                 |
| M3x6mm                    | 2        | Mounts the panel mount into the DFB   |
| Realsense_USB_C_to_C      | 1        | Cable                                 |
| Oak_USB_A_to_C            | 1        | Cable                                 |
| STO_Switch                | 1        |                                       |
| Hip_Return_to_Rus_STO_DFB | 1        | Cable                                 |
| Rus_to_Fei-Fei            | 1        | Cable                                 |
| NUC_Ext_Ethernet_Access   | 1        | Cable                                 |
| IMU                       | 1        | Cable                                 |
| Realsense Camera          | 1        |                                       |

1.  Install the IMU. {value=8}

    A. Secures to the underside of the DFB with x3 M2x16mm bolts and
    complementary nuts.

    IMU DFB Bottom View

    IMU DFB Internal Cavity View

2.  Install the NUC.

    A. It's recommended to plug the NUC to RUS power cable in-advance and bend
    it as the port is on the backside of the NUC.

    Prepped NUC with Power Cable

    B. Fastens to the backside of the DFB with x4 M3x6mm bolts.

    Staging NUC for Installation

    C. Route the power cable to the right-side DFB and plug into the RUS. Take
    caution not to crush the cable or apply pressure to NUC components.

    NUC Power Route

    D. Route the antenna cables thusly.

    NUC Antenna 1

    NUC Antenna 2

    E. Plug in the Power Button from step #2 into the NUC.

    NOTE: *Some* of the power buttons cables still have all eight pins. Make
    sure the top two pins are exposed as demonstrated to prevent damaging the
    NUC.

    How the Power Button Plugs Into NUC

    F. Apply additional zip-ties for strain-relief and cable-management.

3.  Install and connect the Hopper and XBee:

    A. Install the Hopper PCBA to the left side of the DFB with x4 M3x6mm bolts.

    Hopper on DFB

    B. Plug it into the XB (wireless transceiver) on top. *Take care not to bend
    the delicate pins!* Plug in the STO antenna from step #4.

    XB plugged in

    Cabling for DFB

    C. The Rus_to_Hopper cable (*grey cable*) goes around the backside of the
    DFB and across the heat-sink into the Rus PCBA.

    Hopper to RUS STO board

    Hopper to RUS STO behind NUC

    Hopper to RUS STO across heat sink

4.  Install the NUC's USB to Ethernet adaptor and the outgoing ECAT. {value=11}

    A. Zip-tie the Ethernet adaptor in-place and plug it into the NUC.

    Ethernet adaptor Installed

    Adaptor Plugged into NUC

    B. Plug in the NUC_ECAT_DFB cable (*three-headed split cable*) into the
    Ethernet adaptor dongle and snake it around the front of the DFB and across
    the Rus heat-sink into the appropriate slot.

    RUS STO Loop DFB 14A

    NUC Eth to Rus STO

    C. Apply additional zip-ties for stability, strain-relief, and improved
    cable management.

5.  Install the USB Panel Mount plate and its associated cables.

    The USB Panel Mount and Parts

    A. The Panel Mount fastens into the DFB with x2 M3x6mm bolts.

    Mounting the USB Panel

    B. The other ends of the panel mount connectors go across the RUS heat sink
    and plug into the NUC.

    USB Cables into NUC 1

    C. Zip tie the cables lying across the heat sink and to keep the bundles
    together.

    Heat Sink Zip Ties

6.  Install the STO button, tighten the retention nut, and plug it into the 'STO
    But' port on the Rus.

    STO Button into Rus

7.  Install the Rus outward-bound STO ECAT cable.

    A. Hip to RUS STO DFB 20B (*longest blue ECAT cable*) plugs into the Rus STO
    line as shown...

    Rus STO outbound

    B. ...loops over the NUC...

    Rus Outbound STO across NUC

    C. ...around the DFB backside until it is anchored on the DFB left side.
    Anchoring Outbound STO

    Finalize Outbound STO

8.  Install the RUS to FeiFei power cable and zip-tie the parallel bundles
    together.

    Rus to Fei-Fei Power Cable

9.  Install the Ethernet Access port.

    A. Kept in-place with x1 M3x20mm and nut. *The cable will “push” adjacent
    cables and keep them under tension so they don’t fall into the fans.*

    B. Plugs into the remaining NUC Ethernet port on the right side of the DFB.
    Robot Tether Installed

10. Wiring up the IMU.

    nuc to imu

11. Finalizing antenna placements and angle upward. {value=18}

    Antenna Left Internal DFB

    Antenna Right Internal DFB

### Torso

#### Parts Needed

| Part Name | Quantity | Description & Details |
| --- | :---: | --- |
| Torso | 1 | |
| Luxonis Board | 1 | USB camera controller and driver |
| OAK FFC Cable | 1 | Ribbon cable connecting Luxonis Board and |
:                       :          : Oak Camera module.                        :
| Fei-Fei PCBA          | 1        | Power distribution board; v0.3 Rev2; GPN: |
| M3x5mm SHCS           | 4        | Larger bolts for the Fei-Fei              |
| Combined Face Plate   | 2        | Horizontal cross-section of the torso     |
:                       :          : shell; covers the front and back side     :
| Leg Retention Washers | 4        | Blue steel open-ended rings that provide  |
:                       :          : cleat-attachment structure                :
| M4x16mm BHCS          | 14       | Rounded cap screws for attaching endcap   |
:                       :          : plates to chassis                         :
| M4x22mm SHCS          | 8        | Long bolts                                |
| M4 Square Nuts        | 8        | Square nuts that go with the 22mm long    |
:                       :          : bolts                                     :
| M2x5mm SHCS           | 4        | Smaller diameter bolts for Luxonis        |

1.  Starting with an empty chassis shell:

NOTE: Confirm the M4 heat-inserts are pre-installed and mounting holes should be
tapped and reamed in-advance.
Prepped Torso Shell

1.  Install the Luxonis board: {value=2}

    Luxonis PCBA Only

    A. Plug the ribbon cable into the CAMB-2L slot on the backside of the PCBA.

    Ribbon Cable into Lux

    B. Ribbon cable is snaked through the frontside torso channels like so.
    **Carefully bend the FRC, making sure you don't damage the delicate cable.**

    Torso ribbon Cable

    C. Bolt the PCBA down with x4 M2x5mm bolts until finger-tight.

2.  Install the FeiFei board:
    Fei-Fei Only

    Note: The images below show an older variant of the Fei-Fei board without
    connectors to power the actuated head. If you are planning to use the
    actuated head, make sure to install a Fei-Fei board with spare XT30
    connectors.

    A. Position the FeiFei board at its designated location in the torso.
    Boards in Torso Before Bolts

    B. Secure the board with x4 M3x5mm thread-forming bolts until finger-tight.

NOTE: Confirm final positions of the both Luxonis & Fei-Fei before proceeding.
Two Boards Attached to Torso

1.  Install the Combined Face Plates. {value=4}

    A. Align the face plate to the front/back of the torso, and use x4 M4x22mm
    long bolts and their respective square bolts on the outer edges.

    B. Use x7 M4x16mm button-headed bolts to fasten the plate's center-mass to
    the torso.

    C. Perform the same action for the other side of the torso.

Note: For installing the static and actuated head, three M4x16 bolts on the
front face will need to be removed. See above pic.

NOTE: Example of a completed Torso Assembly ready to be populated.
Completed Torso

### Trimotor Assembly

Three "mono motors" combine to form the 1. Abduction, 2. Hip, and 3. Knee joint
for a trimotor.
Three Motors Form a Trimotor

*In a later section,* four different trimotors, each built up to one of four
specific orientations (FR, FL, HL, & HR) forms the quadruped.

There's a lot of overlapping parts and fasteners, so for clarity of process
we'll separate this into THREE DISTINCT PHASES; each adds another component onto
the previous phase, making it more complete as we go along.

1.  **PHASE 1** - "Build Abduction Joint"
2.  **PHASE 2** - "Add Hip Motor"
3.  **PHASE 3** - "Install Cable Harness & Attach Knee"

#### Parts Needed for PHASE 1: "Build Abduction Joint"

| Part Name | Quantity | Description & Details |
| --- | :---: | --- |
| Completed | 1 | Assembled and calibrated via these |
: "Monomotor"    :          : [instructions](actuator_assembly_and_setup.md) :
: Assembly       :          :                                                :
| Abduction Hip  | 1        | Ring-like metal piece                          |
: Bracket        :          :                                                :
| 3⌀3x5mm dowel  | 4        | x2 to hold the hard stop block in place and x2 |
: pins           :          : more that will index us onto the abduction     :
:                :          : motor                                          :
| Bracket End    | 1        | Machined metal piece; complement to the        |
: Stop Block     :          : ring-like bracket piece                        :
| M4x16mm SHCS   | 2        | Bolts for securing the end stop block to the   |
:                :          : bracket input                                  :
| Thrust         | 1        | Matte grey plastic ring that sits between the  |
: washer/bearing :          : hip bracket and the abduction                  :
| Blue steel     | 1        | Another component of the physical hardstop     |
: crescent part  :          :                                                :
| M3x5mm SHCS    | 4        | Secures the endstop onto the abduction motor's |
:                :          : outer ring                                     :
| M4x8mm SHCS    | 6        | Secures bracket into the abduction motor       |

#### Procedure: "Build Abduction Joint"

1.  Combine the abduction bracket with its physical end stop.

    Machined Parts for Abduction Bracket

    A. Press x2 pins into the two smooth bore openings on the hip bracket.
    *These will keep the end stop piece in-place.*

    Abduction Bracket Pins 1&2

    B. Install the remaining two pins onto the "underside" of the abduction
    bracket using the custom fixture. *These will be additional anchors to keep
    the motor secured.

    Abduction Bracket Press Fixture
    Abduction Bracket Pins 3&4

    C. Place the end stop, indexing with the smooth holes atop of the previously
    installed dowels.

    D. Start working x2 M4x16mm bolts into place with some Loctite 243 (*blue*)
    and then torque them down to 3nM.

    Bolting Down Abduction Hardstop

2.  Install the hard stop piece to a trimotor.

    A. Place the spacer/washer in-place before securing the hard stop. **DO NOT
    FORGET THIS PIECE!**

    Monomotor with Washer

    B. Line up the notches on the monomotor and the hard stop crescent piece as
    demonstrated.

    Monomotor hard stop crescent piece only
    Indexing Features on Single Motor and Hard Stop

    C. Apply 243 Loctite (*blue*), install x4 M3x5mm bolts, and torque to 2Nm.

3.  Attach a completed abduction bracket to the prepared mono-motor.

    A. Line up the pins on the bracket underside and openings on the motor
    topside as shown.

    Lining up the pins on the bracket with the monomotor

    B. Confirm the relative positions of the end stop piece and the hard stop
    crescent to ensure the motor has a full range of motion.

    visual aid

    C. Install x6 M4x8mm bolts to hold the bracket in-place atop of the washer
    (*strongly advised to use a ball-tipped hex driver*) with Loctite 243
    (*blue*).

    D. Torque to 3Nm; once in a star pattern and then around the world just to
    be certain it's secured.

Note: **CHECKPOINT #1** - Finished the Abduction Motor Joint. Manually rotate
the joint from end-to-end to confirm smoothness of motion.

Abduction Motor Joint Only

#### Parts Needed for PHASE 2: "Add Hip Motor"

| Part Name | Quantity | Description & Details |
| --- | :---: | --- |
| Abduction Motor Joint | 1 | Complete sub-assembly from PHASE 1 |
| M3x8mm SHCS | 8 | Bolts for the "cleat" system |
| Cleats | 4 | Metal tabs used to secure motors and |
:                         :          : allow ease-of-service                   :
| Thrust Bushing          | 1        | Matte grey plastic ring that keeps the  |
:                         :          : joint flush                             :
| Left/Right Output Plate | 1        | Designates a trimotor assembly as a     |
:                         :          : Left or Right leg                       :
| ⌀3x5mm dowel pins       | 2        | Used as an indexing feature for the L/R |
:                         :          : output plate                            :
| M4x8mm SHCS             | 6        | Secures output plate into hip motor     |

#### Procedure: "Add Hip Motor"

1.  Install another single motor onto the abduction motor assembly. This will
    serve as the HIP MOTOR.

    A. Line up the assets as demonstrated.

    Lining Up Hip 1

    B. One indexing feature is the board cluster port on the monomotor and the
    opening on the abduction bracket output.

    Lining Up Hip 2

    C. Tabs should line up as shown.

    Lining Up Hip 3

2.  Secure hip using the CLEAT system as explained.

    A. x4 cleats and x8 M3x8mm bolts (*no loctite needed; often disassembled*).
    Staged Elements: Hip Motor and Cleats

    B. These are torqued to 2 Nm and oriented so that the metal tabs move
    clockwise, applying force into the motor circumference.

    Orientation of Cleat System Demonstrating Torque Direction

3.  Assigning "leggedness" with the appropriate knee output plate.

    Preparing to install a LEFT knee output plate

    A. Before installation, place another washer on top of the hip motor output;
    *this will keep the plate level and rotating smoothly.

    Washer on Hip Motor Before Knee

    B. Output plate should be pinned with the same 3x5mm's we've been using.

    Pressing Pins Into Output Plate

    C. Line up the pins on the output plate with the smooth bore holes on the
    hip motor. Make sure the endstops allow for full range-of-motion as shown.

    How the Hard Stops and End Stops Align

    D. Plate is bolted onto the motor shaft with M4x8mm x6 and Loctite 243
    (*blue*). Torque in a star-pattern to 2Nm.

    Front Right Leg with Knee Output Plate Front View

NOTE: **CHECKPOINT #2** - Side view of an Abduction and Hip Two-Motor Assembly.
*At this stage the apparatus has been designated either a Right or Left leg and
should be clearly marked accordingly.*
Front Right Leg with Knee Output Plate Side View

#### Parts Needed for PHASE 3: "Install Cable Harness & Attach Knee"

| Part Name                                       | Quantity | Description  |
:                                                 :          : & Details    :
| ----------------------------------------------- | :------: | ------------ |
| Abduction + Hip Two-Motor Assembly              | 1        | Designated a |
:                                                 :          : Left or      :
:                                                 :          : Right leg in :
:                                                 :          : the previous :
:                                                 :          : phase        :
| Cable Harness aka [hip                          | 1        | Needs to     |
: cover](hipcover_assembly_instructions)          :          : match the    :
:                                                 :          : L/R          :
:                                                 :          : designation; :
:                                                 :          : determines   :
:                                                 :          : front or     :
:                                                 :          : hind         :
:                                                 :          : orientation  :
| Additional                                      | 1        | This will be |
: [**monomotor**](actuator_assembly_and_setup.md) :          : the knee     :
:                                                 :          : actuator     :
| M3x8mm SHCS                                     | 14       | x8 go to the |
:                                                 :          : cleat        :
:                                                 :          : system; x4   :
:                                                 :          : to attach    :
:                                                 :          : hip cover,   :
:                                                 :          : x2 to the    :
:                                                 :          : knee gland   :
| "Cleats"                                        | 4        |              |

WARNING: Advised to place the two-motor assembly onto something soft (*e.g. yoga
foam, as shown in the visual aid*) during installation procedure in order to
avoid damaging the various electrical components.

Parts for the final step of trimotor assembly

#### Procedure: "Install Cable Harness & Attach Knee"

1.  Install the hip cover.

    WARNING: Confirm that both the two-motor assembly and the hip cover are the
    same Left or Right orientation before proceeding. Also, MARK THE ASSEMBLY on
    the outside so you know it's final designation as a Front or Hind leg.

    Rear Right Harness and Rear Right Two-Motor Assembly

    A. Plug the cables that run into the cover into the hip boards. Make sure
    that the ECAT cable labelled "I" goes into the Cortes **I**nput and "O"
    plugs into **O**utput, respectively.

    Plugging in Hip Cover

    B. Orienting ECAT and power cables to minimize pinching and/or damaging the
    PCBA!

    Closing the Hip Cover & Routing Bundles

    C. Secure cover to output shell with x4 M3x8mm bolts tightened by hand.

    Bolting down hip cover

2.  Plug in the Abduction motor Power and Cortes Output only! *This PCBA will
    face **into** the torso when we start attaching legs in a later step.*

Plugging Harness into Abduction

Close-up of Plugging Harness into Abduction

1.  Install the knee motor. {value=3}

    A. Secure the knee gland that runs out from the hip cover onto the knee
    output shell/plate with x2 M3x8mm bolts to hand-tightness.
    Securing the Knee Gland

    B. Feed the cables through the hole and towards where the knee motor will be
    installed.
    Ready to Install the Knee

    C. Plug the knee Cortes power along with the ECAT Input and Output.
    Knee Motor Plugged In

    D. Maneuver the cable bundle so it's not crushing any board components or
    twisting the cables beyond a reasonable amount.
    Fitting the Knee Cable Bundle

    E. Output plate and motor heat sink have corresponding tabs that only allow
    one way for the components to mate.
    Knee Alignment

    F. Secure the knee motor with the cleat system x4 and the last required x8
    M3x8mm bolts.

NOTE: CHECKPOINT #3: Fully Completed Trimotor with Cable Harness Assembly. Once
the harness is installed, we have finalized Front or Hind leg orientation on top
of Right or Left nature from the previous phase.

Knee Cleated to the Structure

Alternative View of completed trimotor

Completed Trimotor from internal torso perspective

## Combining Modules

### Installing Trimotors

#### Parts Needed

Preparing to Assemble Torso

| Part Name | Quantity | Description & Details |
| --- | :---: | --- |
| Barkour Torso Assembly  | 1 | Populated with power and camera PCBAs;  |
:                         :          : output plates installed                 :
| Trimotor Assembly       | 4        | One configured for **F**ront **L**eft   |
:                         :          : (FL), **F**ront **R**ight (FR),         :
:                         :          : **H**ind **R**ight (HR), and **H**ind   :
:                         :          : **L**eft (HL)                           :
| Cleats Retention System | 16       | Secures the leg to the torso output     |
:                         :          : plate                                   :
| M3x8mm SHCS             | 40       | x32 Bolts reserved for the cleat        |
:                         :          : system; each metal tab requires x2 to   :
:                         :          : secure. Remaining x8 are used to attach :
:                         :          : the leg cable grommets into the torso.  :

> Note: Staging the front and rear leg pairs so we can better visualize how it's
> all coming together. Front Left is first in line and will plug into the Deep
> Fry Basket. These elements are closer to the power distribution board and
> thusly have shorter power cables.

> Preparing to Install Front Legs to Torso

> Hind legs will complete the circuit back into the DFB. These have the longer
> power cables because they have to travel farther to reach the Fei-Fei PCBA.
> Hind Left is the last trimotor in the chain.

> Ready to Install Hind Legs to Torso

#### Procedure

1.  Attach the **Front Left** Trimotor.

    A. This plugs directly into the DFB and is therefore is the first "leg" on
    the device chain.

    B. Take note of the orientation of the grommet cable bundle coming from the
    trimotor and how it slots into the torso.
    Marking the Torso Grommet Mounting Points

    C. Secure the torso grommet to the designated slot with x2 M3x8mm bolts.

    D. Use the cleat system to keep the leg attached to the torso. Each leg
    takes x4 of the metal tabs and x8 M3x8mm bolts. Torque all to 2Nm.

    E. It should look like the example below.

    Front Left Installed Only

2.  Connecting the **Front Right** Trimotor.

    A. Mount and secure the trimotor using the same channels as before to align
    the torso; *it should be the same as FL but mirrored*.

    Both Front Trimotors Installed

    B. Plug the outgoing SS (**S**ame **S**ide) cable from the FL (*see previous
    step #1*) into the FR abduction Cortes Input slot.

    C. Plug in the FL and FR Fei-Fei connectors into the power distribution
    board; *their designations are clearly marked on the PCBA.*

    visual aid

3.  Moving down to the **Hind Right** Trimotor.

    A. Slot in the torso grommet and secure trimotor to torso with the same
    aforementioned cleat system.

    Installing hind right torso grommet

    HR secured with cleats

    B. Plug the outgoing OS (**O**pposite **S**ide) cable from the FR (*see
    previous step #2*) into the HR abduction Cortes Input.

    My ECAT cables goes across the room and starts to drink your ECAT

    C. Plug the longer Fei-Fei cable into the power distribution board, as
    shown.

    Three out of Four Power Distro

4.  Finishing installation with **Hind Left** Trimotor.

    A. Seat, cleat, and complete the HL leg into the torso.

    Installing the Last Leg, Hind Left

    B. The outgoing SS (**S**ame **S**ide) cable from HR (_see previous step #3
    _) travels BEHIND the scaffolding as shown before plugging into the HL
    Cortes Input.

    visual aid

    visual aid

    C. Fourth verse, same as the last three: plug HL into power distribution. We
    should now have a complete & unbroken ECAT chain from FL that runs
    counter-clockwise all the way to HL.

> NOTE: Now we're ready to attach the rest of the legs onto the robot. **SECURE
> INTERNAL WIRING BEFORE CONTINUING** with some zip ties, as shown.
>
> Location 1: *inside the torso, by the FL trimotor's abduction Cortes*
> visual aid
> Location 2: *FR's outgoing OS cable*
> visual aid
> Location 3: *robot right side internal rail*
> visual aid

### Completing the Legs

#### Parts Needed

Staging Leg Stuff for the Final Installation

| Part Name  | Quantity | Description & Details |
| --- | :---: | --- |
| Torso | 1 | Assembled Torso with all four attached & wired |
: assembly   :            : trimotor assemblies                                :
| Leg        | 4          | Basically the "thigh, calf, and foot" analog for   |
: linkages   :            : the robot; you need x2 **L**eft designation and x2 :
:            :            : **R**ight designation for a full assembly; [refer  :
:            :            : to sub-page for assembly                           :
:            :            : instructions](leglinkage_assembly_instructions.md) :
| Inner      | 4 (2 left  | Serves as the frame to connect the leg linkage     |
: Thigh      : & 2 right) : into a knee motor.                                 :
: Shell      :            :                                                    :
| Outer      | 4 (2 left  | Complementary "shell" piece that will enclose the  |
: Thigh      : & 2 right) : leg linkage.                                       :
: Shell      :            :                                                    :
| Knee half  | 4          | Connects lower leg to thigh shells.                |
: pin        :            :                                                    :
: cleareance :            :                                                    :
| Knee half  | 4          | Connects lower leg to thigh shells.                |
: pin tapped :            :                                                    :
| ⌀3x5mm     | 20         | Every outer shell gets x5; used as additional      |
: dowel pins :            : indexing to keep the shell pairs secured.          :
| M3x6mm     | 32         | Fastens the inner R/L thigh shell onto the         |
: SHCS       :            : corresponding R/L knee output; x8 per leg.         :
| M4x8mm     | 24         | Secures leg linkage crank into the knee motor      |
: SHCS       :            : output; x6 per leg.                                :
| Bumper     | 4          | Rubber pad to protect against shell-on-shell       |
:            :            : violence.                                          :
| M3x20mm    | 12         | Holds the inner and outer shells together; x3 per  |
: SHCS       :            : leg.                                               :
| M3x10mm    | 20         | Same as above; x5 per leg.                         |
: SHCS       :            :                                                    :
| M5x40mm    | 4          | Secures the knee half pins.                        |
: FHCS       :            :                                                    :

#### Procedure

1.  Press x5 dowel pins into the designated holes in the outer thigh shell with
    some Loctite 243 (*blue*) for additional stability.

    Dowel pins in the left outer shell

2.  Secure the inner shell onto the knee motor output.

    A. Place the inner thigh shell onto the knee motor.

    Thigh on knee

    WARNING: For alignment, line up the notches on the thigh inner shell with
    the notches on the heatsink. **There are specific details for whether the
    leg is in the Front or Hind region!**

    Thigh Shells and Trimotor Alignment Examples

    B. Once placements are finalized, apply Loctite 243 (*blue*) and install
    with x8 M3x6mm screws around the perimeter of the motor and torque to 2Nm.

    Thigh screws

3.  Install the appropriate Right or Left linkage into the motor and shell.

    A. Place the linkage on the thigh and motor, making sure the dowel pins are
    aligned with the holes on the face of the motor, and the slot on the crank
    is aligned with the slot in the motor. Apply Loctite 243 (*blue*) and
    install onto the motor inner-ring with x6 M4x8mm bolts torqued down to 3Nm.

    Linkage bolted onto motor

    C. Ensure full-range of motion from one hard stop to the other before
    proceeding to the final steps.

    Leg fully extended                                                                | Leg fully closed
    :-------------------------------------------------------------------------------: | :--------------:
    Leg full extension | Leg full closed

4.  Secure the outer motor plate.

    A. Place a rubber bumper stop into the inner thigh at the provided slot.

    Bumper stop staging

    Bumper stop in-place

    B. Align and press the outer & inner thigh shells to make sure everything
    lines up. Then install with x3 M3x20mm bolts to finger-tightness in order to
    keep the halves together, but allow for ease of service.

    Shell Long Bolts

    C. On the backside, further secure halves together with x5 M3x10mm bolts,
    once again, to finger-tightness. This leg is now fully assembled.

    Backside Shell Bolts

5.  Fasten the knee.

    A. Adjust the lower leg so that the flanged ball bearing is centered with
    the outer shell knee holes.
    Aligned knee holes

    B. Slot in the tapped and clearance half pins into the knee hole and fasten
    with an M5x40mm hex flathead bolt.

    Knee Pin Clearance                                                              | Knee Pin Tapped
    :-----------------------------------------------------------------------------: | :-------------:
    Knee Clearance | Knee Tapped

6.  Repeat steps 1 through 5 for each of the leftover leg designations
    {value=5}.

> NOTE: It should look like this after all four legs have been assembled.
> Finished "Leggy" All legs
> should have full range-of-motion on all joints
> Finished "Leggy" Alt View
> Take notice the cable management and ensure no exposed connectors or stray
> cables are left unsecured inside the torso.
> Finished "Leggy" Topside Looking In

### Final Assembly

#### Parts Needed

| Part Name | Quantity | Description & Details |
| --- | :---: | --- |
| Assembled Torso | 1 | A *mostly complete* Barkout Robot |
:                           :          : with all four trimotors attached and  :
:                           :          : wired into the torso along with leg   :
:                           :          : extensions                            :
| Assembled Deep-Fry Basket | 1        |                                       |
| Handle                    | 1        | Means to carry the Barkour Robot      |
| Handle Pin                | 2        | Keeps the handle secured to the torso |
:                           :          : and prevents the DFB from escaping    :
| Neck                      | 1        | 3D-printed extension for the neck;    |
:                           :          : houses the outgoing USB cable         :
| M4x16mm BHCS              | 1        | Fastens the output plate into the     |
:                           :          : torso heat insert                     :
| M4x20mm BHCS              | 3        | Secures the neck into the torso       |
| Head                      | 1        | 3D-printed bracket that holds the USB |
:                           :          : camera in-place                       :
| M3x8mm SHCS               | 12       | Securing the head/face plate onto the |
:                           :          : neck once the usb camera is           :
:                           :          : installed; also for the secondary     :
:                           :          : camera block to the handle            :
| OAK camera                | 1        | Cube-shaped camera that plugs into    |
:                           :          : the Luxonis PCBA with a ribbon cable  :
| Camera mount              | 1        | Cubicle-like mount for the OAK camera |

#### Procedure

1.  Installing the Deep Fry Basket (DFB) into the "Leggy" Torso.

    A. Align the two assets as shown, using the four indexing tabs.

    Aligning Four Features on DFB to Torso

    B. Plug in the ECAT chain. The front side of the DFB has an outgoing
    receptacle that plugs into the abduction Cortes on the **F**ront **L**eft
    trimotor assembly. The backside of the DFB (*consult visual aid*) receives
    the last connection from **H**ind **L**eft hip return, completing the STO
    loop.

    DFB Backside completes STO line

    C. Plug in the Luxonis USB and RUS to Fei-Fei power cables.

    How Luxonis and Fei Fei connect to DFB

    D. Ensure that the ribbon cable from the Luxonis board has an unobstructed
    path out of the torso. *This will become relevant later.*

    Path of the Luxonis cable coming out of the Torso

    E. Slide the basket into the torso, making sure no cables are pinched in the
    process. ***It should sit flush with the rest of the torso shell.***

2.  Installing the Neck (*and Head*).

    Two Views of an Alpha Neck

    A. Neck will be mounted onto the front-side output plate as shown:

    Mounting Neck into Torso

    B. First, use a single M4x16mm bolts at position 4 (*it will be unreachable
    once the neck is installed in the next phase.*)

    C. Then put the 3D-printed neck piece in-place and bolt it down down with x3
    M4x20mm bolts (*longer*) at positions 1-3.

    Neck Attached to Torso

3.  Finalizing placement of the head and camera.

    A. The DFB has an outgoing USB-C cable that snakes through an opening in the
    neck frame.

    Close-up of Camera Cable Opening

    DFB USB Cable Only

    B. It will interface with the camera at an angled connector, as shown in
    isolation.

    Camera Connected to USB DFB Only

    C. Fasten the faceplate over the camera and onto the neck output with the x8
    M3x8mm bolts.

    AP Camera Front View

    How camera is installed, two views

4.  Attaching the handle and secondary camera.

    A The ribbon cable from the Luxonis board will snake through the sole
    opening in the handle and towards the secondary camera installed on the
    handle.

    Plugging in Secondary Camera

    B. Install the camera into its 3D-printed shell and then fasten to the
    handle with x4 M3x8mm bolts.

    C. Line up the hole on the handle and the torso shell before using both
    pinions to secure it in-place.

    Handle Pinned to Torso

> NOTE: View of the final assembly:
> Complete Barkour 1
>
> Complete Barkour 2

## Starting Up the Robot

Plug in a battery pack into the slot in the deep fry basket.

1.  Remove one (or both) of the handle pinions in order to access the slot for
    power.

2.  Slot in a Dewalt battery pack, making sure the leads line up.
    Dewalt Battery, LEDS on

3.  The robot should power on without needing to press the power button.

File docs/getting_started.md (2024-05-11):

# Getting Started with the Barkour Robots

### STO (Safe Torque Off/E-Stop)

Each robot has two E-stops connected in series: a wireless E-stop (big red
button) and a button on the robot (green light). To enable torque, the red
button must be disengaged (twist it to make it pop up) and the STO button on the
robot must be pressed in. If these conditions are met, the light inside the STO
button on the robot will light up. If the green light on the robot is on, the
torque is enabled (i.e. robot can move).

IMPORTANT: The wireless STO should always be engaged (*i.e. pushed in*) whenever
the robot is not in active use (*e.g. before or after an experiment, or while
you take a break, etc.*).

USAGE NOTES:

1.  Prioritize pressing the red external button for safety purposes.

    Wireless E-stop

2.  When things go wrong, push in the wireless E-stop. **Do not** attempt to
    reach the button on the robot's back; this is unsafe on the best of days.

3.  The button on the back is there to make sure a user can force the torque off
    while they are near the robot (*i.e. prevent anyone else from making the
    joints move*).
    On-robot STO

4.  The two buttons are wired in series.

5.  The button should be lit up (*i.e. green*) for the motors to work

    Green LED on E-Stop Indicates Ready to Use

    A. The button on the DFB should be depressed.

    B. And the wireless red button is disengaged.

6.  If you find an unattended robot and its STO is not engaged, err on the side
    of caution and please press the wireless E-stop button.

To power/charge the wireless E-stop, connect it to a USB-C power supply.

### Battery Insertion

Make sure the wireless STO is pressed before inserting the battery (torque off).

To insert a battery, remove the pin from the robot's hind side (you have to push
on the pin's end, while pulling it out), then lift up the handle. Drop the
battery inside the battery holder and make sure you hear a click. After a few
seconds the blue light (power symbol) will turn on (this is the onboard
computer). Lower the handle (the yellow strap should stick out through the
battery ). Replace the hind pin.

Important: Never operate the robot without the handle or without having both
handle pins secured. Doing so will damage the hardware.

Important: The battery voltage is 60V. Do not touch the red or black power
cables inside the robot/motor drivers. If you hear something rattling inside the
torso, immediately shut down the robot and remove the battery (loose metal
objects + electricity == bad).

### Battery Removal

Make sure the wireless STO is pressed before removing the battery (torque off).

Remove the pin from the robot's hind side, then lift up the handle. Push the
black button on the battery do disconnect it from the battery connector and pull
gently on the yellow strap to lift up the battery a bit. Then pull out the
battery.

Important: Remove the battery from the robot when you are done. Do not leave a
battery inside the robot or allow it to drain fully.

### Battery Swap

Make sure the wireless STO is pressed before swapping the battery (torque off).

It is possible to do a battery swap while keeping the onboard computer
powered on. To do so, connect a battery to the external yellow XT30 connector
(right next to the battery slot). Then follow the instructions to remove the
robot's battery and insert a new battery. Finally, remove the external battery.

The onboard computer will remain powered on during the procedure, but the motors
will be powered off.

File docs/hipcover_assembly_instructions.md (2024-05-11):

# Hip Cover & Cable Harness Sub-Assembly

[TOC]

## Overview

The hip cover is a complex scaffolding and wiring structure that tunnels power
and signal from the torso of the robot into the trimotor assemblies and back.

NOTE: In the partially-assembled robot below, we have a Front Right leg (*screen
left*) with the hip cover installed compared to a leg sans cover (*right side*).
The entire hip cover and cable harness sub-assembly is highlighted purple.
Side-by-side Example of Leg with Hip Cover Installed vs Barren Leg

This is the path upon which ECAT signal travels down. It starts from the torso,
and next proceeds into the abduction, then into the hip, and finally terminating
at the knee before returning to the torso.

NOTE: An inside and outside view of a hip cover and its cable harness assembly.
*Parts have been highlighted to group them with regards to direction &
orientations.*
Hip Cover Inside and Outside View
Everything highlighted **BLUE** resides inside the hip. \
**RED** is used to denote the external hip features. \
The **GREEN** bundle travels through a center hole in the cover into the knee. \
And the **YELLOW** group funnels through the topside hole into the torso.

And it comes in FOUR DISTINCT BUILD CONFIGURATIONS:

1.  **FL** \(**F**ront **L**eft\)
2.  **HL** \(**H**ind **L**eft\)
3.  **FR** \(**F**ront **R**ight\)
4.  **HR** \(**H**ind **R**ight\)

This dictates the specific lengths of cables needed to cross over the physical
space inside the robot in order to reach power and communication.

## Parts Needed

Separating the inventory chart into three distinct "chunks" so we can better
parse how the disparate power and signal cables come together based on the
specific assembly configuration we are making.

### EtherCAT Cables

Five cables are involved in I/O for the EtherCAT signal.

| Part Name | Quantity | Description & Details |
| --- | :---: | --- |
| A2H ECAT | 1 | Transfers data from **A**bduction to (**2**) |
:                    :          : **H**ip Gebru; Cable 15                      :
| H2K ECAT           | 1        | Communication between **H**ip to (**2**)     |
:                    :          : **K**nee PCBAs; Cable 16                     :
| K2H Cover ECAT     | 1        | One half of the "return cable" from **K**nee |
:                    :          : through the **H**ip *and back into the       :
:                    :          : torso*; Cable 17                             :
| Hip Return SS ECAT | 1/0      | Second half of the "return cable"; used if   |
:                    :          : the following leg is on the **S**ame         :
:                    :          : **S**ide; Cable 18                           :
| Hip Return OS ECAT | 0/1      | Alternative complement for "return cable" if |
:                    :          : the next joint is on the **O**pposite        :
:                    :          : **S**ide; Cable 19                           :

WARNING: Front Left (FL) and Rear Left (RL) have special incoming and outgoing
cables dependent on the (DFB) that are NOT LISTED HERE (see cable drawings). The
reason being that FL and RL are the first and last limb in the ECAT chain,
respectively.

### Power Distribution Cables

Three distinct cables are used for power distribution.

| Part Name | Quantity | Description & Details |
| --- | :---: | --- |
| Hip Power Distro  | 1 | Cable 4; plugs directly into the Fei-Fei PCBA |
:                   :          : so **all build configurations will use ONE of :
:                   :          : these**                                       :
| Fei-Fei to A+H FR | 1/0      | Distributes power to **A**bduction and        |
:                   :          : **H**ip; exclusively used for **FR**ont legs; :
:                   :          : Cable 2                                       :
| Fei-Fei to A+H RE | 0/1      | Only for **RE**ar cable assemblies; Cable 3   |

Three Unique Power Cables for the Hip Cover

WARNING: Do not repair faulty cables. If a pin is loose or sleeving is damaged
or connectivity is suspect, cut and **throw away** the cable.

### Mechanical Parts

The mechanical components will be the same regardless of the previous cable
combinations.

| Part Name | Quantity | Description & Details |
| --- | :---: | --- |
| Hip Cover | 1 | 3D printed part that shields the hip  |
:                        :             : PCBA;                                 :
| Cable Clamps           | 2           | Complementary archpieces to the hip   |
:                        :             : cover that serve as cable retention   :
| M3x12mm FHCS           | 4           | Countersunk bolt that secures the     |
:                        :             : cable clamps into the hip-cover heat  :
:                        :             : inserts                               :
| Braided Cable Wrapping | *as needed* | For organizing the cable bundles; we  |
:                        :             : cut two pieces per harness\: 180mm x1 :
:                        :             : and 250mm x1                          :
| Torso Grommet          | 1           | Paired 3D-printed parts that retain   |
:                        :             : the bundle to torso                   :
| M3x10mm SHCS           | 2           | Secures torso grommet mated pieces    |
| Knee Cable Entry Gland | 1           | Two mated 3D-printed pieces that      |
:                        :             : retain the cable running into the     :
:                        :             : knee                                  :
| M3x18 FHCS BO          | 2           | Counter-sunk bolts that keeps the     |
:                        :             : knee gland parts together             :

## Procedure

1.  Combine the appropriate power cable pair and affix it to the left side of
    the internal Hip Cover.

    A. Staring with various empty Hip Covers. *In this example we've already
    specified limb designation in advance for the entire batch based on build
    need.*

    Hip Covers Only with Designations

    NOTE: We have a cover meant for a **Front Left** leg so the following
    procedure will be based on that particular build configuration. *The
    necessary heat inserts should already be installed.*
    Hip Cover FL

    B. It will receive the corresponding pair: x1 `Hip Power Distro` and x1
    `Fei-Fe to A+H FR`
    Front Left Fei Fei Cable Pair

    C. Secure the junction of the power cable pair with a zip-tie around the
    `XT60H-M`(ale) connector as shown. Slowly tighten with a zip-tie gun to
    approximate tightness setting: 2.5
    FL Power Cable Zip tied
    Close-up FL Power Cable Pair

2.  Assemble the corresponding ECAT "return cable" duo and affix it to the
    right-side slot of the internal Hip Cover.

    NOTE: Mark all ends with their corresponding **I**nput or **O**utput
    (*arbitrary designation*) so they don't get mixed up or plugged in the wrong
    direction once finalized.
    Input and Output

    A. The current limb is Front Left (FL). *Therefore the following joint must
    be Front Right (FR)*, which is on the SAME SIDE. **Thus we use the required
    x1 `K2H Cover ECAT` along with a x1 `Hip Return SS ECAT`**

    NOTE: The "return cable" with a mark to denote the junction between a `K2H`
    cable and either a `SS` or `OS` cable, depending on what specific leg comes
    next.
    Paired Return Cable

    B. Secure the junction on the remaining right-side slot with a zip-tie
    across the `Molex 2014441110` as shown and tighten to spec like before.
    Return ECAT Zip Tied

3.  Slot in the Abduction (output side) to Hip (input side) Ethercat cable.

    A. `A2H ECAT` goes in through he topside hole from the outside.
    Abduction into Hip Input through Hip Cover

    B. We zip-tied it on the external side to preserve bundle length.
    A2H Minimum Length Zip Tied (internal view)

    *It will need ~3 inches into the motor in order to properly reach the hip
    Gebru*.
    A2H Minimum Length Zip Tied (External view) with partial view of H2K

4.  Install the Hip (output end) to Knee (input) Ethercat cable. A. The `H2K
    ECAT` cable will tunnel from inside the hip cover and through the middle
    opening to the outside.

    H2K Minimum Length Zip Tied

    B. *This goes further downstream into the KNEE joint, which is last in the
    trimotor chain.*

5.  Wrap and secure the external cable bundles.

    A. Cut a pair of braided cable sleeving to lengths of 180mm and 250mm.
    Cable Sleeve 180mm
    Cable Sleeve 250mm

    B. Wrap the external cable bundles as shown.

    NOTE: The shorter 180mm length will exit to topside hole and run towards the
    torso. The longer 250mm variant covers the cables coming out from the center
    hole and into the knee.
    Cable Bundles, Lengths, and Directions

    C. Ensure the ends of the bundles are slightly crossing through the openings
    so the clamps will secure them in the following step.

    D. Each hole exiting the hip cover has a complementary clamp piece that is
    secured with x2 m3x12mm bolts. Tighten until the cable feels anchored.
    Secured Cable Clamps

NOTE: For the following steps we'll be applying the additional scaffolding for
the cable bundle outputs. In the below example we have a torso grommet pair
(*left*) and the knee gland assembly. (right).
Grommet and Wallace Parts
*Prior to the installation we cut out two aluminum rods to 120mm and 190mm in
order to serve as "rulers" to ensure enough slack for cables to reach their
intended destinations.*
Aluminum 120mm Guide Into Torso
Aluminum 190mm Guide Into Knee

1.  Install the Torso Grommet {value=6}

    A. Confirm distance before marking and clamping. Make sure the cables aren't
    all tangled up inside the bungle, which could lead to pinched wires.
    Measuring for Torso Grommet

    B. Also consider the **ORIENTATION** of the mated halves, as they need to be
    installed as shown to easily slot into the torso with minimal cable strain.
    Torso Grommet Orientation

    C. Clamp the halves together, aligning openings to heat inserts, and
    screwing down x2 M3x10mm bolts to hand-tightness.
    Grommet Secured Close-up

2.  Apply Knee Entry Gland

    A. Measure distance and access cable "health" as before.
    Measuring for Knee Gland

    B. Confirm orientation of the knee gland pieces with respect to the cable
    bundle, as shown:
    Knee & Cable Orientation

    WARNING: The knee gland pieces can be connected incorrectly. This creates a
    much tighter opening which can damage the cable bundle going into the knee
    *on top of* not properly fitting into the joint it's traveling towards.
    Knee Gland Pairs Wrong vs Correct

    C. Clamp down the knee gland pairs and fasten the x2 M3x18mm bolts to
    hand-tightness.

NOTE: Example of a completed **F**ront **L**eft (**FL**) hip cover & cable
harness sub-assembly. REMEMBER: there are minor differences with regards to
cable lengths, combinations, and port orientation depending on which specific
leg you are building for.
Completed Front Left Hip Cover & Cable Harness

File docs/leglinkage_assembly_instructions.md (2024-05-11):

# Leg Linkage Sub-Assembly

[TOC]

NOTE: This is the part that connects into the trimotor. There is a **L**eft and
**R**ight version based on the specific knee crank installed.

## Parts needed per leg

| Part Name | Quantity | Description & Details |
| --- | :---: | --- |
| Linkage | 1 | Long bar with openings on both |
:                                 :          : ends                           :
| Knee Crank                      | 1        | Engraved with **L** or **R**   |
:                                 :          : depending on which side is     :
:                                 :          : being assembled                :
| ⌀3x5mm Dowel Pin                | 2        | Allows the knee crank to index |
:                                 :          : with the motor output          :
| Linkage half pin clearance      | 2        | Part of the pin that connects  |
:                                 :          : linkage to knee crank          :
| Linkage half pin tapped         | 2        | Same as above                  |
| Stainless Steel Ball Bearing    | 4        | Inserts into the linkage       |
| Flanged Ultra-Thin Ball Bearing | 2        | Inserts into the lower leg     |
| Lower Leg                       | 1        |                                |
| Bumper Piece                    | 1        | Rubber "knee" pad              |
| Foot                            | 1        | Rubber padding with pawprint   |
| M4x22mm FHCS                    | 2        | Connects the linkage half pins |

## Assembly steps

NOTE: This assembly is for a **left leg**.

1.  Install x4 bearings (*two on each end*) into a single linkage.

    A. Lightly apply Loctite 638 (*green*) to the outer circumference of the
    bearing and hand-press into place.

    Apply Loctite

    B. Give each some time to cure before proceeding.

    Linkage with Bearing

2.  Install a knee crank onto one end of the completed linkage.

    NOTE: This step assigns **R**ight or **L**eft "leggedness" based on the
    markings on the metal.
    L&R Knee Cranks

    A. Press x2 ⌀3mm dowel pins into the holes on the back of the knee crank as
    shown:
    Right Knee Crank with Pin

    B. Fasten the crank to the linkage using a pair of clearance and tapped
    linkage half pins, and x1 M4x22mm countersunk bolt dabbed with Loctite 262
    (*red*). **The tapped half pin should be on the back side of the knee crank.
    See images below.**

    Knee Crank Front                                                                         | Knee Crank Back
    :--------------------------------------------------------------------------------------: | :-------------:
    Attaching Link to Crank 1 | Attaching Link to Crank 2

    C. It needs to be tight enough for **no wobble** but smooth axial motion.
    Swing the axle end-to-end to assess the full range of motion.

3.  Prepare the lower leg piece for attachment.

    A. Attach the flanged ball bearing to both sides of the lower leg. These
    press fit into the leg.
    Lower Leg bearing

    B. Glue the knee bumper piece into the cut-out of the lower leg.
    Lower Leg Bumper

4.  Attach the lower leg piece to the linkage + knee subassembly using the same
    trio of half pins, countersunk bolt, and red Loctite from step #2B. As
    before, confirm by hand whether the joint freely rotates without lateral
    wobble.

    Knee Linkage Parts

5.  Affix foot and complete the leg.

    A. Slide the foot over the lower leg adapter and route the zip ties through
    the channels as shown.

    B. Use a zip tie gun to secure it.

    Ziptie foot

The complete linkage and lower leg should look like the image below.
Lower leg completed

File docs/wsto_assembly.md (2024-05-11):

# Wireless STO Assembly

This document describes the assembly of the wireless safety transmitter and
receiver (WSTO) used with the Barkour Robot. The transmitter, known as Grace, is
a handheld device that can be used to remotely stop a robot in an emergency. The
receiver, known as Hopper, is mounted on the robot and receives signals from
Grace.

[TOC]

## Transmitter Assembly {:#transmitter-assembly}

### Bill of materials

1.  Grace PCBA
2.  Remote E-stop transceiver module (Digi XB3-24Z8UM)
3.  Custom XBee breakout board
4.  WSTO cover lid
5.  WSTO cover base
6.  Remote E-stop portable power bank (TNTOR WT-H369)
7.  Remote E-stop power bank cable (Xiwai UC-096-UP-0.13M-XY)
8.  Remote E-stop antenna (Digi A24-HABUF-P5I-ND)
9.  Remote E-stop button (IDEC XA1E-BV404-R)
10. M3 x 20mm countersunk screws (qty 2)
11. Brass Tapered Heat-Set Inserts M3 x 0.5mm thread, 3.8mm length (qty 2)

WSTO transmitter

WSTO transmitter without its lid

### Grace PCBA

The electronics design files for Grace are in `hardware/electronics/Grace.zip`.

The Grace PCBA is custom made, whereas the XBee and its sockets are available
off-the-shelf. The XBee sockets are through-hole, single-row, 10-way, 2mm; we
use [Sparkfun PRT-8272][2]{:.external}, but any part meeting specifications is
acceptable. The specific XBee used is the Digi XBee3 PRO (MPN: XB3-24Z8UM).

Grace PCBA

### Remote E-stop transceiver module

The XBee transceiver on Grace acts as a transmitter.

XBee

We used a custom board to mount the XBee. However, an off-the-shelf board is
acceptable as long as it has the correct dimensions.

XBee breakout board

*XBee shown soldered onto custom breakout board*

### E-Stop button

[Instruction sheet (external link)][3]{:.external}

E-stop button

The E-stop button is panel-mounted. To install it, follow these steps:

1.  Remove the red button from the E-stop
2.  Position the E-stop in the WSTO housing
3.  Clamp the E-stop with a nut onto the housing
4.  Replace the red button

The E-stop wires are terminated with a Molex nanofit 105307-1206.

#### Contact arrangements (bottom view)

E-stop terminals

E-stop wiring

### Antenna

The antenna is mounted to the WSTO housing as shown in
[this image](#wsto-no-lid). The pigtail cable connects to the XBee.

Antenna

### Portable power bank

The portable power bank is located within the WSTO transmitter housing, beneath
the Grace PCBA. It has 1 USB-A output port and 1 USB-C input and output port.

Power bank

### Portable power bank cable

Power bank cable

The USB-A end of the power bank cable plugs into the portable power bank. The
USB-C end of the cable plugs into the Grace PCBA.

### WSTO transmitter housing

The plastic WSTO transmitter housing is a custom made, 3D printed part. Holes
for the antenna, E-stop button, etc. are included in the design, so no drilling
is required.

## Receiver Assembly {:#receiver-assembly}

### Bill of materials

1.  Hopper PCBA
2.  M3 x 12mm cap head screw (qty 4)
3.  Rus to Hopper cable
4.  On-robot E-stop antenna (Abacon PRO-EX-296)
5.  Remote E-stop transceiver module (Digi XB3-24Z8UM)
6.  Custom XBee breakout board

### Hopper PCBA

The electronics design files for Hopper are in
`hardware/electronics/Hopper.zip`.

XBee headers will likely need to be soldered by hand after the PCBA is
delivered. The M3 screws are used to mount the PCB to the robot. Hopper
uses the TPS54331 buck converter circuit used on Cortes.

Hopper PCBA

Hopper XBee

### Remote E-stop transceiver module

The XBee transceiver on Hopper acts as a receiver. For photos, refer to the
[Grace section](#xbee).

### On-robot E-stop antenna

This antenna receives the STO signal from the WSTO transmitter assembly.

On-robot E-stop antenna

Partially installed on-robot E-stop antenna

Fully installed on-robot E-stop antenna

*Antenna as installed in the DFB*

## XBee Programming and Documentation {:#xbee-programming}

### XCTU

XBees are configured with Digi International's XCTU software tool. This allows
firmware updates and parameter configuration via serial communication with the
XBee. The program is available for Linux, macOS, and Windows.

[XCTU product page and download][7]{:.external}

### Connect the XBee to the host

XBee devices can be configured via any serial to USB connection. We use the
SparkFun [XBee Explorer USB][8]{:.external} breakout for simplicity. This allows
the XBee to be seated in the breakout and connected directly to the host
computer via a mini-USB cable. In this setup, XCTU can detect and reprogram the
XBee without any additional hardware or changes.

To connect the XBee to the host computer, follow these steps:

1.  In the XCTU window, click **Add devices**

XCTU Add devices

1.  In the dialog, click **Finish** {value=2}

XCTU dialog

### Update the firmware

To update the XBee firmware, follow these steps:

1.  Click the **Radio Configuration** tab
2.  From the **Radio Configuration** pane, click **Update**

XCTU update

1.  In the **Update firmware** dialog, select **XB3-24 > Digi XBee3 802.15.4 >
    200D (Newest)** {value=3}
2.  Click **Update**

XCTU update dialog

### Configure the Grace and Hopper XBee parameters

To configure the Grace (transmitter) and Hopper (receiver) XBee parameters,
follow these steps:

1.  Connect the Hopper XBee to your computer
2.  Note the **Serial Number High** and **Serial Number Low** values (**SH** and
    **SL**) of the Hopper XBee

XCTU SH and SL parameters

1.  For Grace, set the parameters as shown in the table below: {value=3}

| Parameter | Parameter Value | Notes |
| --- | --- | --- |
| CH | `19` | |
| ID | `XXXX` | Give it a unique PAN ID (for |
:           :                             : example\: `AAFA`)                  :
| MM        | **Strict 802.15.4 no ACKs   |                                    |
:           : \[1\]**                     :                                    :
| NI        | `TX_XXX`                    | Give it a unique, sequential       |
:           :                             : number (for example\: `TX_101`)    :
| MY        | `FFFF`                      |                                    |
| DH        | **Serial Number High** from | Usually `0013A200`                 |
:           : paired Hopper               :                                    :
| DL        | **Serial Number Low** from  |                                    |
:           : paired Hopper               :                                    :
| PL        | **Highest \[4\]**           | This may not be available based on |
:           :                             : the XBee model                     :
| CA        | `0`                         |                                    |
| RO        | `0`                         |                                    |
| PT        | `14`                        |                                    |

Note: All other parameters use the default values

1.  Click **Write** {value=4}

XCTU write

1.  Note the **SH** and **SL** of the Grace XBee {value=5}
2.  For Hopper (receiver), set the parameters as shown in the table below:

| Parameter | Parameter Value | Notes |
| --- | --- | --- |
| CH | `19` | |
| ID | `XXXX` | Give it the same PAN ID as paired  |
:           :                             : Grace above (for example\: `AAFA`) :
| MM        | **Strict 802.15.4 no ACKs   |                                    |
:           : \[1\]**                     :                                    :
| NI        | `RX_XXX`                    | Give it the same number as Grace   |
:           :                             : above (for example\: `RX_101`)     :
| MY        | `FFFF`                      |                                    |
| DH        | **Serial Number High** from | Usually `0013A200`                 |
:           : paired Grace                :                                    :
| DL        | **Serial Number Low** from  |                                    |
:           : paired Grace                :                                    :
| PL        | **Highest \[4\]**           | This may not be available based on |
:           :                             : the XBee model                     :
| CA        | `0`                         |                                    |
| RO        | `0`                         |                                    |
| PT        | `14`                        |                                    |

Note: All other parameters use the default values

1.  Click **Write** {value=7}

XCTU write

[2]: https://www.sparkfun.com/products/8272
[3]: https://us.idec.com/idec-us/en/USD/medias/B-794-7-E.pdf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
[7]: https://hub.digi.com/support/products/xctu/
[8]: https://www.sparkfun.com/products/11812

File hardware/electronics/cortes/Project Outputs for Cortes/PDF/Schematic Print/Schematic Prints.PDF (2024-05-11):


THIS DESIGN IS BEING PROVIDED FOR
NON-COMMERCIALUSE ONLY. THE USE
OF CORINNA CORTES'S NAME IN
CONNECTION WITH THE DESIGN IS NOT
INTENDED TO IMPLY THAT CORINNA
CORTES SPONSORS OR ENDORSES THE
DESIGN, GOOGLE LLC, OR ANY OF
GOOGLE LLC'S PRODUCTS OR SERVICES.


3D accelerometer, 3D gyroscope, 3D magnetometer VDDIO 1


THIS DESIGN IS BEING PROVIDED FOR


THIS DESIGN IS BEING PROVIDED FOR


One Selectshould be high and the other low

STM32 has native PDM interface

Termination resistorsshould be placed close to driving source

THIS DESIGN IS BEING PROVIDED FOR


NRST has internal 40 kOhm pullup
nRST

"in" "out" and "i/o" is GPIO

IA_ADC

Blinky and Button can also be i2c4
Blinky1 - SMBA
Blinky2 - CLK
nButton - SDA

GD_PWM_HC | PA9 D13 | ECAT_RESET
GD_PWM_LC | PA10 C14 | ENC_CLK

PA11 C15 | ENC_MISO
PA12 B15 | ENC_MOSI

TCK_SWCLK | PA14(JTCK/SWCLK) A12
TDI | PA15(JTDI) A11

JTRST | PB4(NJTRST) B6
VCP_RX | PB5 C6
VCP_TX | PB6 A5 | ECAT_MFCIO_0
ECAT_LATCH_IN1 | PB7 B5 | MIC_DATA

PB14 K15 | ECAT_SYNC_OUT0
PB15 K14 | ECAT_SYNC_OUT1

TR_CLK | PE2 C3
TR_DATA0 | PE3 B2 | FSOE_STO2_CTRLR out

IC_ADC | PF11 N7
VDSA_ADC | PF12 P11

CREATIVE COMMONS PUBLIC LICENSE: CC BY-NC 4.0 THIS DESIGN IS BEING PROVIDED FOR | BARKOUR ROBOT CORTES CONTROLLER | Processor.SchDoc


VSS A15 | D 1 1
C 2
D 6

F 8 | M 5
F 9 | M 9
F | 1 0
F | 1 2

VSS G8

VSS G10
H 6 | | VFBSMPS
H 7 | | | 1 U F 6 . 3 V
H 8

J 6
J 7
J 8 | R 1 | 3

J 1 0
J 1 4

VSS K9 | LV XSM P S
VSS K10
VSS K12 | F | 2.2 u H


MFC and PDI SPI muxed internally.

Weak internal pulldown activates PDI

ECAT0
Port 0 = EtherCAT in, 1 = EtherCAT out

Writes are possible with ~WC is driven low or floating.

No connection per datasheet pg 35

0.1UF A | C39 | VCCIO F10
0.1UF A | C40 | VCCIO F11

C41 | VCCIO G10

1010000b for memory access, 1011000b for identification access

3V3 VDD5_OUT tied to 3v3 per datasheet pg 35

THIS DESIGN IS BEING PROVIDED FOR


30 30 | STO1

To avoid introducing any extra noise, all encoder signals will simply be passed
through Gebru, not using the Gebru GND plane, etc

STO

This is a header for development purposes
which allows for bypassing the STO in the
connector with the onboard 24V. It's
suggested to populate this with a header
which shows it is obviously populated!!

THIS DESIGN IS BEING PROVIDED FOR


THIS DESIGN IS BEING PROVIDED FOR

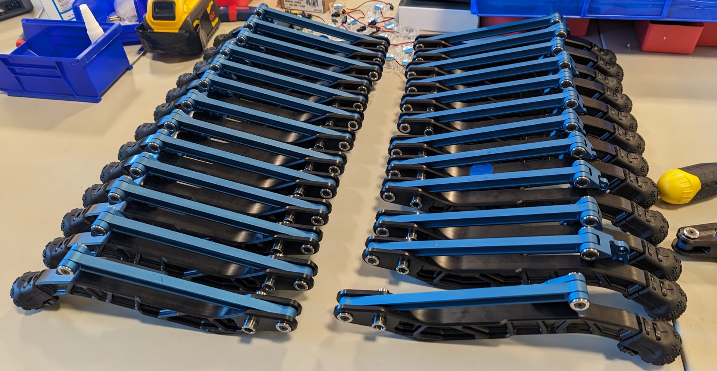
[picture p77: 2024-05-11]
docs/images/robot_assembly/leg/lower_leg_complete_several.jpg

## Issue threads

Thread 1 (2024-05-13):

Holberton Design Files

jaschawilcox, 2024-05-13:
Hello, I see mention of the integrated single board `holberton` motor driver -- however it does not appear to be available in the `hardware/electronics` folder?

kcaluwae, 2024-05-13:
Good catch. I'll try to upload it tomorrow.

kcaluwae, 2024-05-13:
Pushed! Check out hardware/electronics/holberton

Closed 2024-05-13.

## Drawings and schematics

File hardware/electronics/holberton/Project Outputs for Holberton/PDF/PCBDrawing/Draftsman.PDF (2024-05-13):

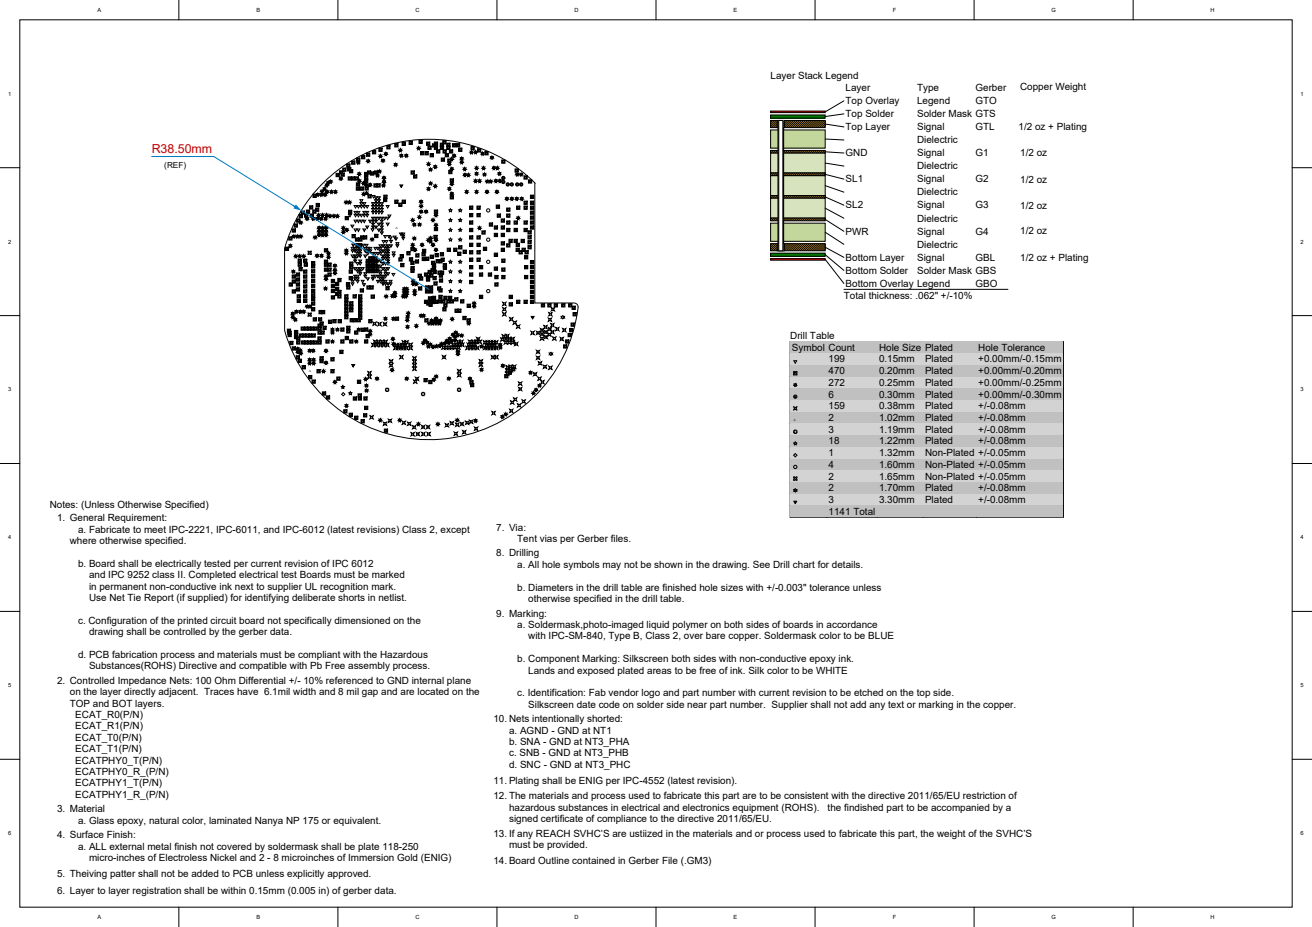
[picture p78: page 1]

Bottom Solder Solder Mask GBS
Total thickness: .062" +/-10%

Notes: (Unless Otherwise Specified)
General Requirement:
a. Fabricate to meet IPC-2221, IPC-6011, and IPC-6012 (latest revisions) Class 2, except
where otherwise specified.

Via:
Tent vias per Gerber files.
Drilling
a. All hole symbols may not be shown in the drawing. See Drill chart for details.

b. Board shall be electrically tested per current revision of IPC 6012
and IPC 9252 class II. Completed electrical test Boards must be marked
in permanent non-conductive ink next to supplier UL recognition mark.
Use Net Tie Report (if supplied) for identifying deliberate shorts in netlist.

b. Diameters in the drill table are finished hole sizes with +/-0.003" tolerance unless
otherwise specified in the drill table.
Marking:
a. Soldermask,photo-imaged liquid polymer on both sides of boards in accordance
with IPC-SM-840, Type B, Class 2, over bare copper. Soldermask color to be BLUE

c. Configuration of the printed circuit board not specifically dimensioned on the
drawing shall be controlled by the gerber data.

d. PCB fabrication process and materials must be compliant with the Hazardous
Substances(ROHS) Directive and compatible with Pb Free assembly process.
Controlled Impedance Nets: 100 Ohm Differential +/- 10% referenced to GND internal plane
on the layer directly adjacent. Traces have 6.1mil width and 8 mil gap and are located on the
TOP and BOT layers.
ECAT_R0(P/N)
ECAT_R1(P/N)
ECAT_T0(P/N)
ECAT_T1(P/N)
ECATPHY0_T(P/N)
ECATPHY0_R_(P/N)
ECATPHY1_T(P/N)
ECATPHY1_R_(P/N)
Material
a. Glass epoxy, natural color, laminated Nanya NP 175 or equivalent.
Surface Finish:
a. ALL external metal finish not covered by soldermask shall be plate 118-250
micro-inches of Electroless Nickel and 2 - 8 microinches of Immersion Gold (ENIG)
5. Theiving patter shall not be added to PCB unless explicitly approved.
6. Layer to layer registration shall be within 0.15mm (0.005 in) of gerber data.

b. Component Marking: Silkscreen both sides with non-conductive epoxy ink.
Lands and exposed plated areas to be free of ink. Silk color to be WHITE

c. Identification: Fab vendor logo and part number with current revision to be etched on the top side.
Silkscreen date code on solder side near part number. Supplier shall not add any text or marking in the copper.
Nets intentionally shorted:
a. AGND - GND at NT1
b. SNA - GND at NT3_PHA
c. SNB - GND at NT3_PHB
d. SNC - GND at NT3_PHC
11. Plating shall be ENIG per IPC-4552 (latest revision).
The materials and process used to fabricate this part are to be consistent with the directive 2011/65/EU restriction of
hazardous substances in electrical and electronics equipment (ROHS). the findished part to be accompanied by a
signed certificate of compliance to the directive 2011/65/EU.
If any REACH SVHC’S are ustiized in the materials and or process used to fabricate this part, the weight of the SVHC’S
must be provided.
14. Board Outline contained in Gerber File (.GM3)

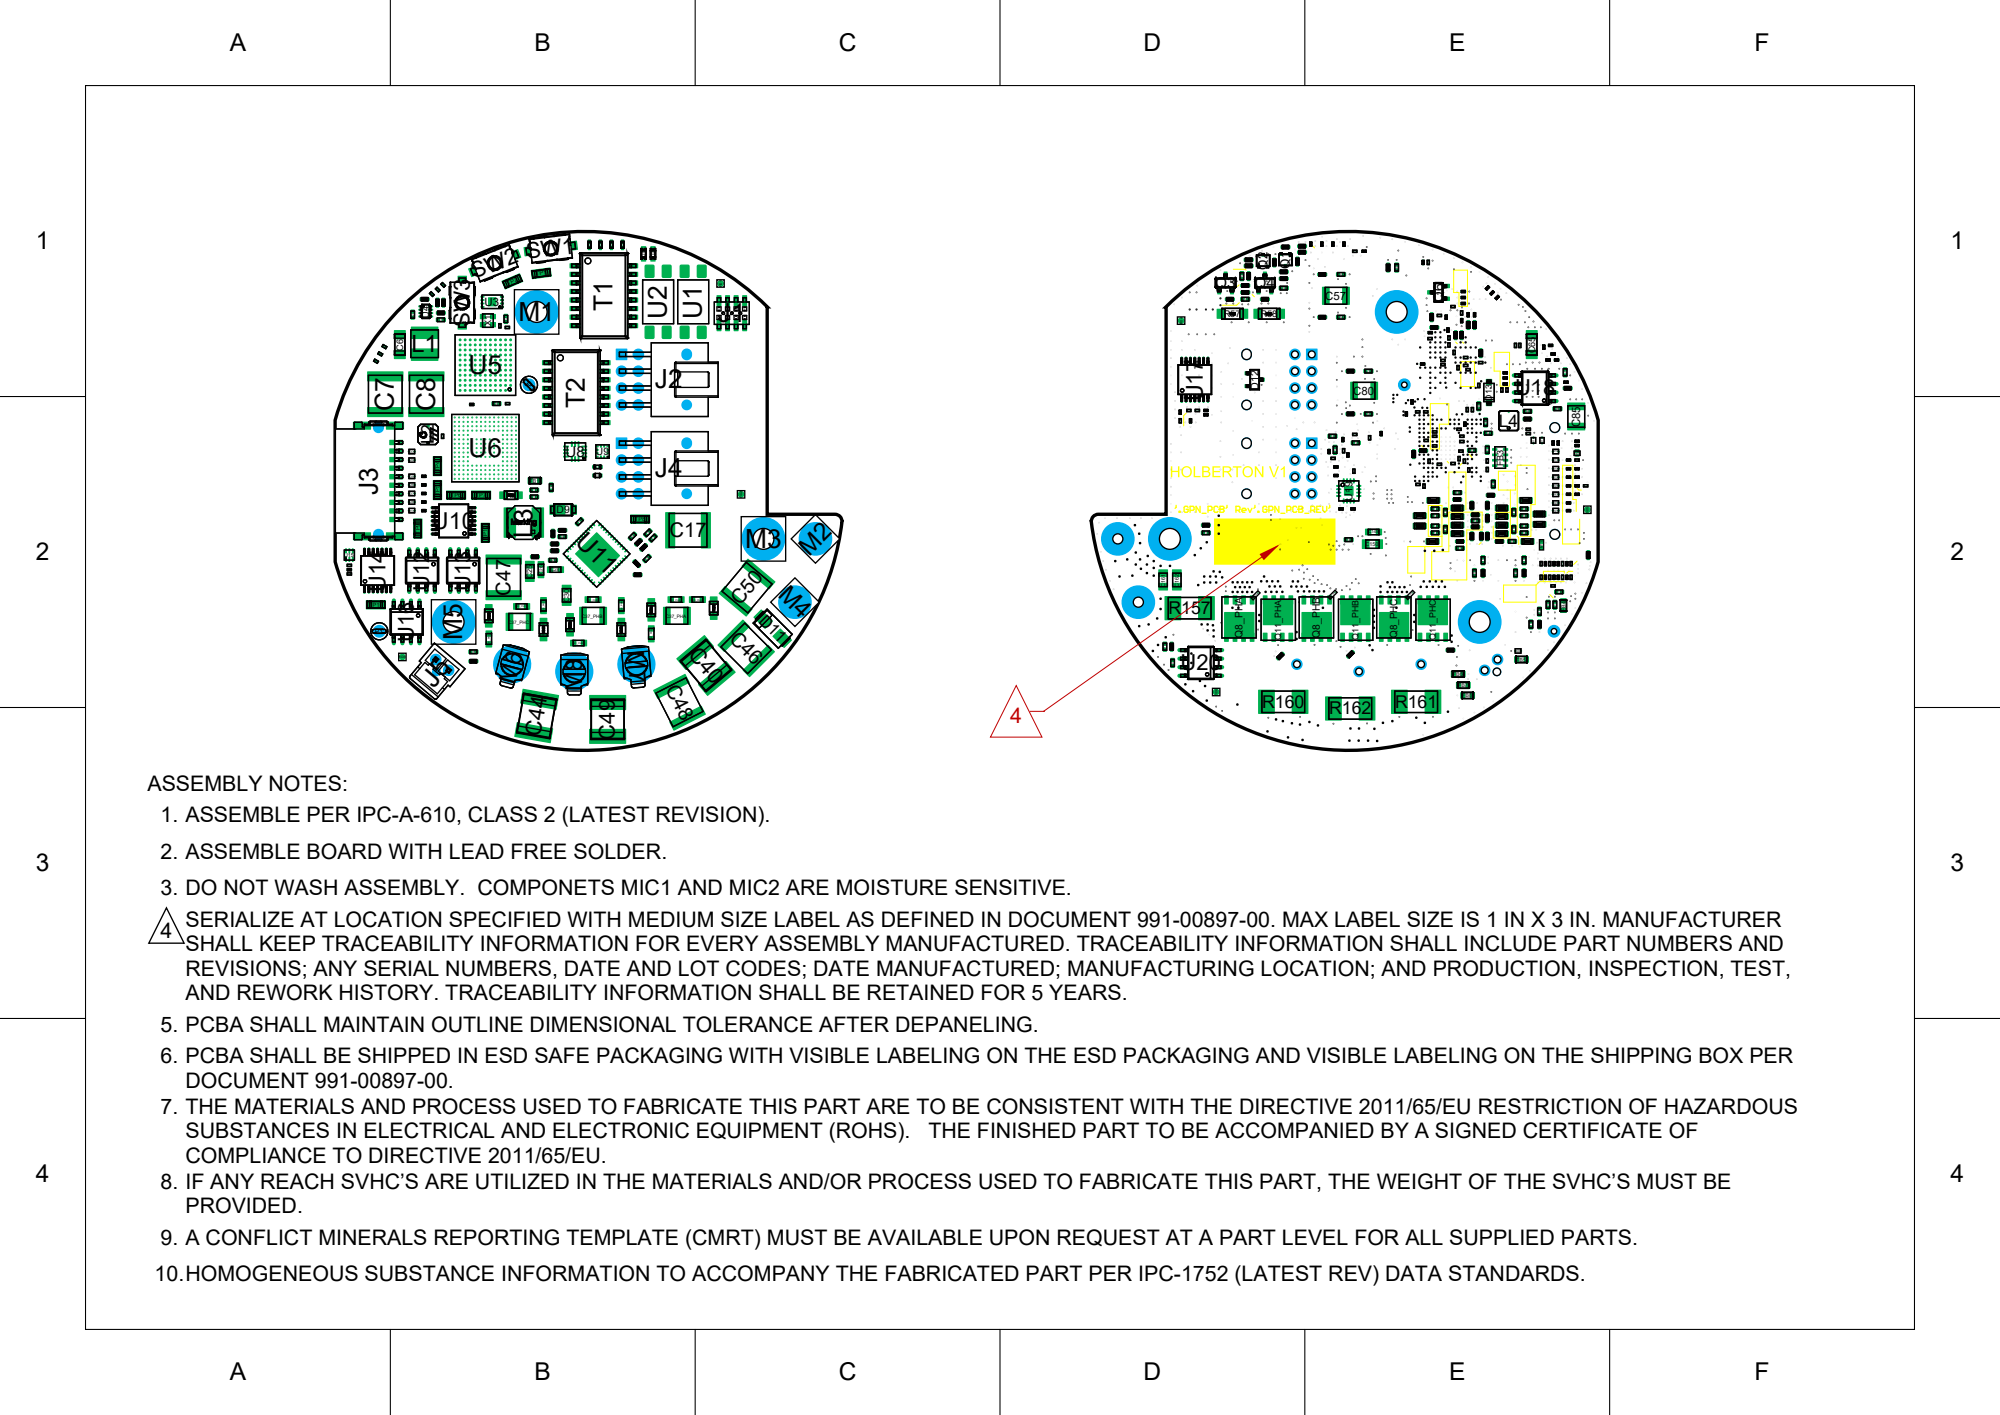
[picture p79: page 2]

ASSEMBLY NOTES:
1. ASSEMBLE PER IPC-A-610, CLASS 2 (LATEST REVISION).
2. ASSEMBLE BOARD WITH LEAD FREE SOLDER.
3. DO NOT WASH ASSEMBLY. COMPONETS MIC1 AND MIC2 ARE MOISTURE SENSITIVE.
SERIALIZE AT LOCATION SPECIFIED WITH MEDIUM SIZE LABEL AS DEFINED IN DOCUMENT 991-00897-00. MAX LABEL SIZE IS 1 IN X 3 IN. MANUFACTURER
SHALL KEEP TRACEABILITY INFORMATION FOR EVERY ASSEMBLY MANUFACTURED. TRACEABILITY INFORMATION SHALL INCLUDE PART NUMBERS AND
REVISIONS; ANY SERIAL NUMBERS, DATE AND LOT CODES; DATE MANUFACTURED; MANUFACTURING LOCATION; AND PRODUCTION, INSPECTION, TEST,
AND REWORK HISTORY. TRACEABILITY INFORMATION SHALL BE RETAINED FOR 5 YEARS.
5. PCBA SHALL MAINTAIN OUTLINE DIMENSIONAL TOLERANCE AFTER DEPANELING.
PCBA SHALL BE SHIPPED IN ESD SAFE PACKAGING WITH VISIBLE LABELING ON THE ESD PACKAGING AND VISIBLE LABELING ON THE SHIPPING BOX PER
DOCUMENT 991-00897-00.
THE MATERIALS AND PROCESS USED TO FABRICATE THIS PART ARE TO BE CONSISTENT WITH THE DIRECTIVE 2011/65/EU RESTRICTION OF HAZARDOUS
SUBSTANCES IN ELECTRICAL AND ELECTRONIC EQUIPMENT (ROHS). THE FINISHED PART TO BE ACCOMPANIED BY A SIGNED CERTIFICATE OF
COMPLIANCE TO DIRECTIVE 2011/65/EU.
IF ANY REACH SVHC’S ARE UTILIZED IN THE MATERIALS AND/OR PROCESS USED TO FABRICATE THIS PART, THE WEIGHT OF THE SVHC’S MUST BE
PROVIDED.
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

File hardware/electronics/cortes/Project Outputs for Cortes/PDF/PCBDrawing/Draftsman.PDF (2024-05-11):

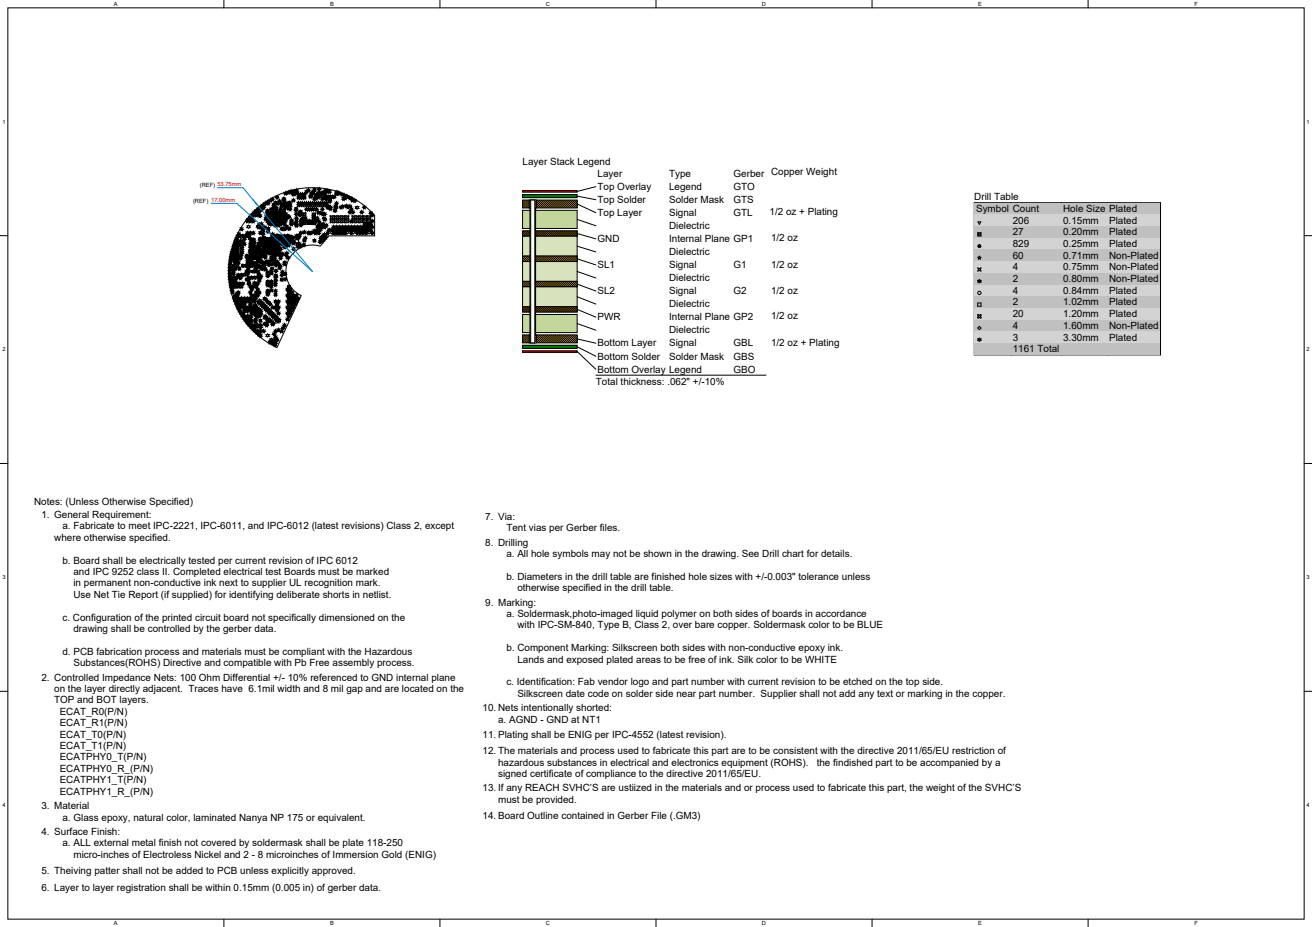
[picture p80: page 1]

Symbol | Count | Hole Size | Plated

206 | 0.15mm | Plated
27 | 0.20mm | Plated
829 | 0.25mm | Plated
60 | 0.71mm | Non-Plated
4 | 0.75mm | Non-Plated
2 | 0.80mm | Non-Plated
4 | 0.84mm | Plated
2 | 1.02mm | Plated
20 | 1.20mm | Plated
4 | 1.60mm | Non-Plated
3 | 3.30mm | Plated
1161 Total

Bottom Solder Solder Mask GBS
Total thickness: .062" +/-10%

Notes: (Unless Otherwise Specified)
General Requirement:
a. Fabricate to meet IPC-2221, IPC-6011, and IPC-6012 (latest revisions) Class 2, except
where otherwise specified.

Via:
Tent vias per Gerber files.
Drilling
a. All hole symbols may not be shown in the drawing. See Drill chart for details.

b. Board shall be electrically tested per current revision of IPC 6012
and IPC 9252 class II. Completed electrical test Boards must be marked
in permanent non-conductive ink next to supplier UL recognition mark.
Use Net Tie Report (if supplied) for identifying deliberate shorts in netlist.

b. Diameters in the drill table are finished hole sizes with +/-0.003" tolerance unless
otherwise specified in the drill table.
Marking:
a. Soldermask,photo-imaged liquid polymer on both sides of boards in accordance
with IPC-SM-840, Type B, Class 2, over bare copper. Soldermask color to be BLUE

c. Configuration of the printed circuit board not specifically dimensioned on the
drawing shall be controlled by the gerber data.

b. Component Marking: Silkscreen both sides with non-conductive epoxy ink.
Lands and exposed plated areas to be free of ink. Silk color to be WHITE

d. PCB fabrication process and materials must be compliant with the Hazardous
Substances(ROHS) Directive and compatible with Pb Free assembly process.
Controlled Impedance Nets: 100 Ohm Differential +/- 10% referenced to GND internal plane
on the layer directly adjacent. Traces have 6.1mil width and 8 mil gap and are located on the
TOP and BOT layers.
ECAT_R0(P/N)
ECAT_R1(P/N)
ECAT_T0(P/N)
ECAT_T1(P/N)
ECATPHY0_T(P/N)
ECATPHY0_R_(P/N)
ECATPHY1_T(P/N)
ECATPHY1_R_(P/N)
Material
a. Glass epoxy, natural color, laminated Nanya NP 175 or equivalent.
Surface Finish:
a. ALL external metal finish not covered by soldermask shall be plate 118-250
micro-inches of Electroless Nickel and 2 - 8 microinches of Immersion Gold (ENIG)
5. Theiving patter shall not be added to PCB unless explicitly approved.
6. Layer to layer registration shall be within 0.15mm (0.005 in) of gerber data.

c. Identification: Fab vendor logo and part number with current revision to be etched on the top side.
Silkscreen date code on solder side near part number. Supplier shall not add any text or marking in the copper.
Nets intentionally shorted:
a. AGND - GND at NT1
11. Plating shall be ENIG per IPC-4552 (latest revision).
The materials and process used to fabricate this part are to be consistent with the directive 2011/65/EU restriction of
hazardous substances in electrical and electronics equipment (ROHS). the findished part to be accompanied by a
signed certificate of compliance to the directive 2011/65/EU.
If any REACH SVHC’S are ustiized in the materials and or process used to fabricate this part, the weight of the SVHC’S
must be provided.
14. Board Outline contained in Gerber File (.GM3)

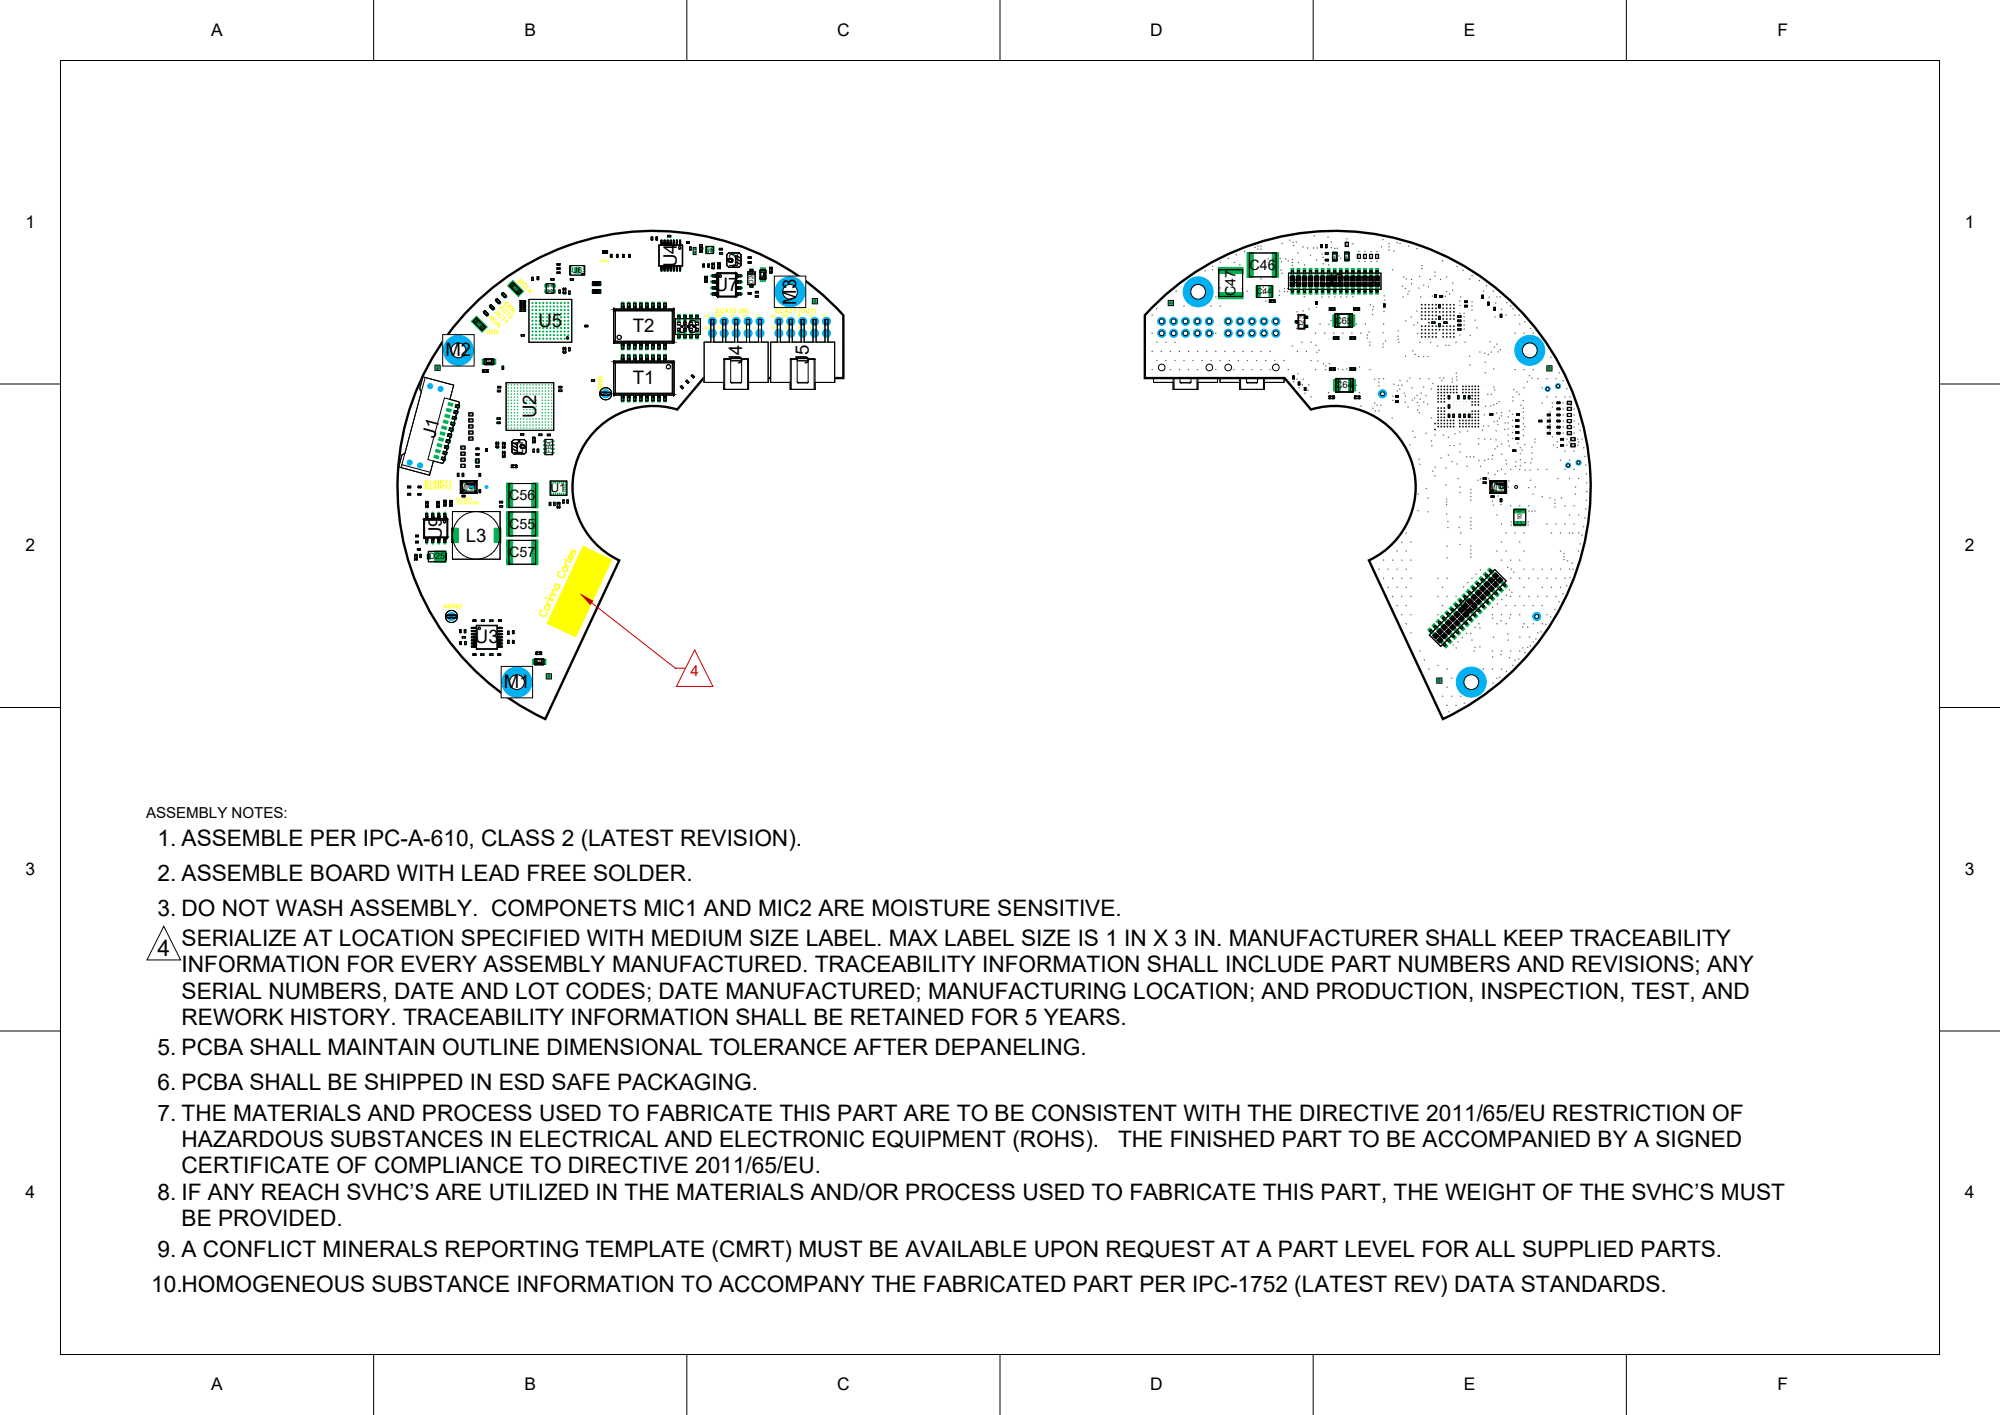
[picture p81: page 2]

ASSEMBLY NOTES:
1. ASSEMBLE PER IPC-A-610, CLASS 2 (LATEST REVISION).
2. ASSEMBLE BOARD WITH LEAD FREE SOLDER.
3. DO NOT WASH ASSEMBLY. COMPONETS MIC1 AND MIC2 ARE MOISTURE SENSITIVE.
SERIALIZE AT LOCATION SPECIFIED WITH MEDIUM SIZE LABEL. MAX LABEL SIZE IS 1 IN X 3 IN. MANUFACTURER SHALL KEEP TRACEABILITY
INFORMATION FOR EVERY ASSEMBLY MANUFACTURED. TRACEABILITY INFORMATION SHALL INCLUDE PART NUMBERS AND REVISIONS; ANY
SERIAL NUMBERS, DATE AND LOT CODES; DATE MANUFACTURED; MANUFACTURING LOCATION; AND PRODUCTION, INSPECTION, TEST, AND
REWORK HISTORY. TRACEABILITY INFORMATION SHALL BE RETAINED FOR 5 YEARS.
5. PCBA SHALL MAINTAIN OUTLINE DIMENSIONAL TOLERANCE AFTER DEPANELING.
6. PCBA SHALL BE SHIPPED IN ESD SAFE PACKAGING.
THE MATERIALS AND PROCESS USED TO FABRICATE THIS PART ARE TO BE CONSISTENT WITH THE DIRECTIVE 2011/65/EU RESTRICTION OF
HAZARDOUS SUBSTANCES IN ELECTRICAL AND ELECTRONIC EQUIPMENT (ROHS). THE FINISHED PART TO BE ACCOMPANIED BY A SIGNED
CERTIFICATE OF COMPLIANCE TO DIRECTIVE 2011/65/EU.
IF ANY REACH SVHC’S ARE UTILIZED IN THE MATERIALS AND/OR PROCESS USED TO FABRICATE THIS PART, THE WEIGHT OF THE SVHC’S MUST
BE PROVIDED.
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

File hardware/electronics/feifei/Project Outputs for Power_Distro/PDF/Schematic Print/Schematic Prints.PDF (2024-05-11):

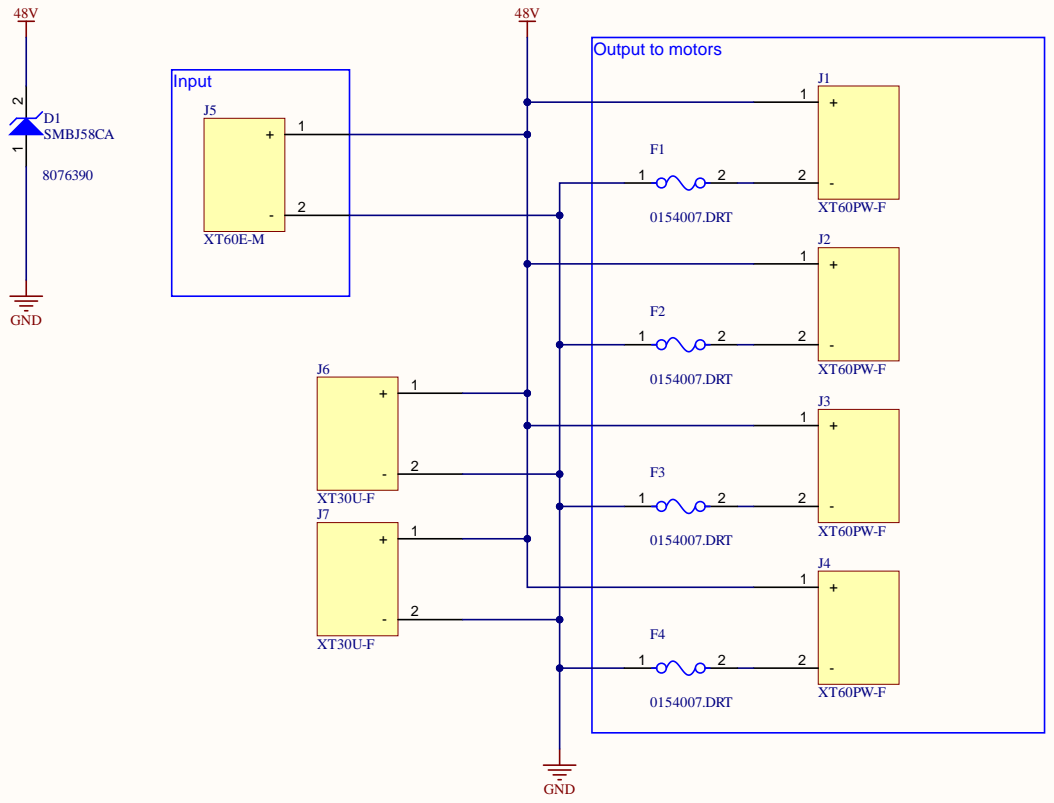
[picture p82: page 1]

FEI-FEI POWER DISTRO

THIS DESIGN IS BEING PROVIDED FOR
NON-COMMERCIALUSE ONLY. THE USE
OF FEI-FEI LI'S NAME IN CONNECTION
WITH THE DESIGN IS NOT INTENDED TO
IMPLY THAT FEI-FEI LI SPONSORS OR
ENDORSES THE DESIGN, GOOGLE LLC, OR
ANY OF GOOGLE LLC'S PRODUCTS OR
SERVICES.

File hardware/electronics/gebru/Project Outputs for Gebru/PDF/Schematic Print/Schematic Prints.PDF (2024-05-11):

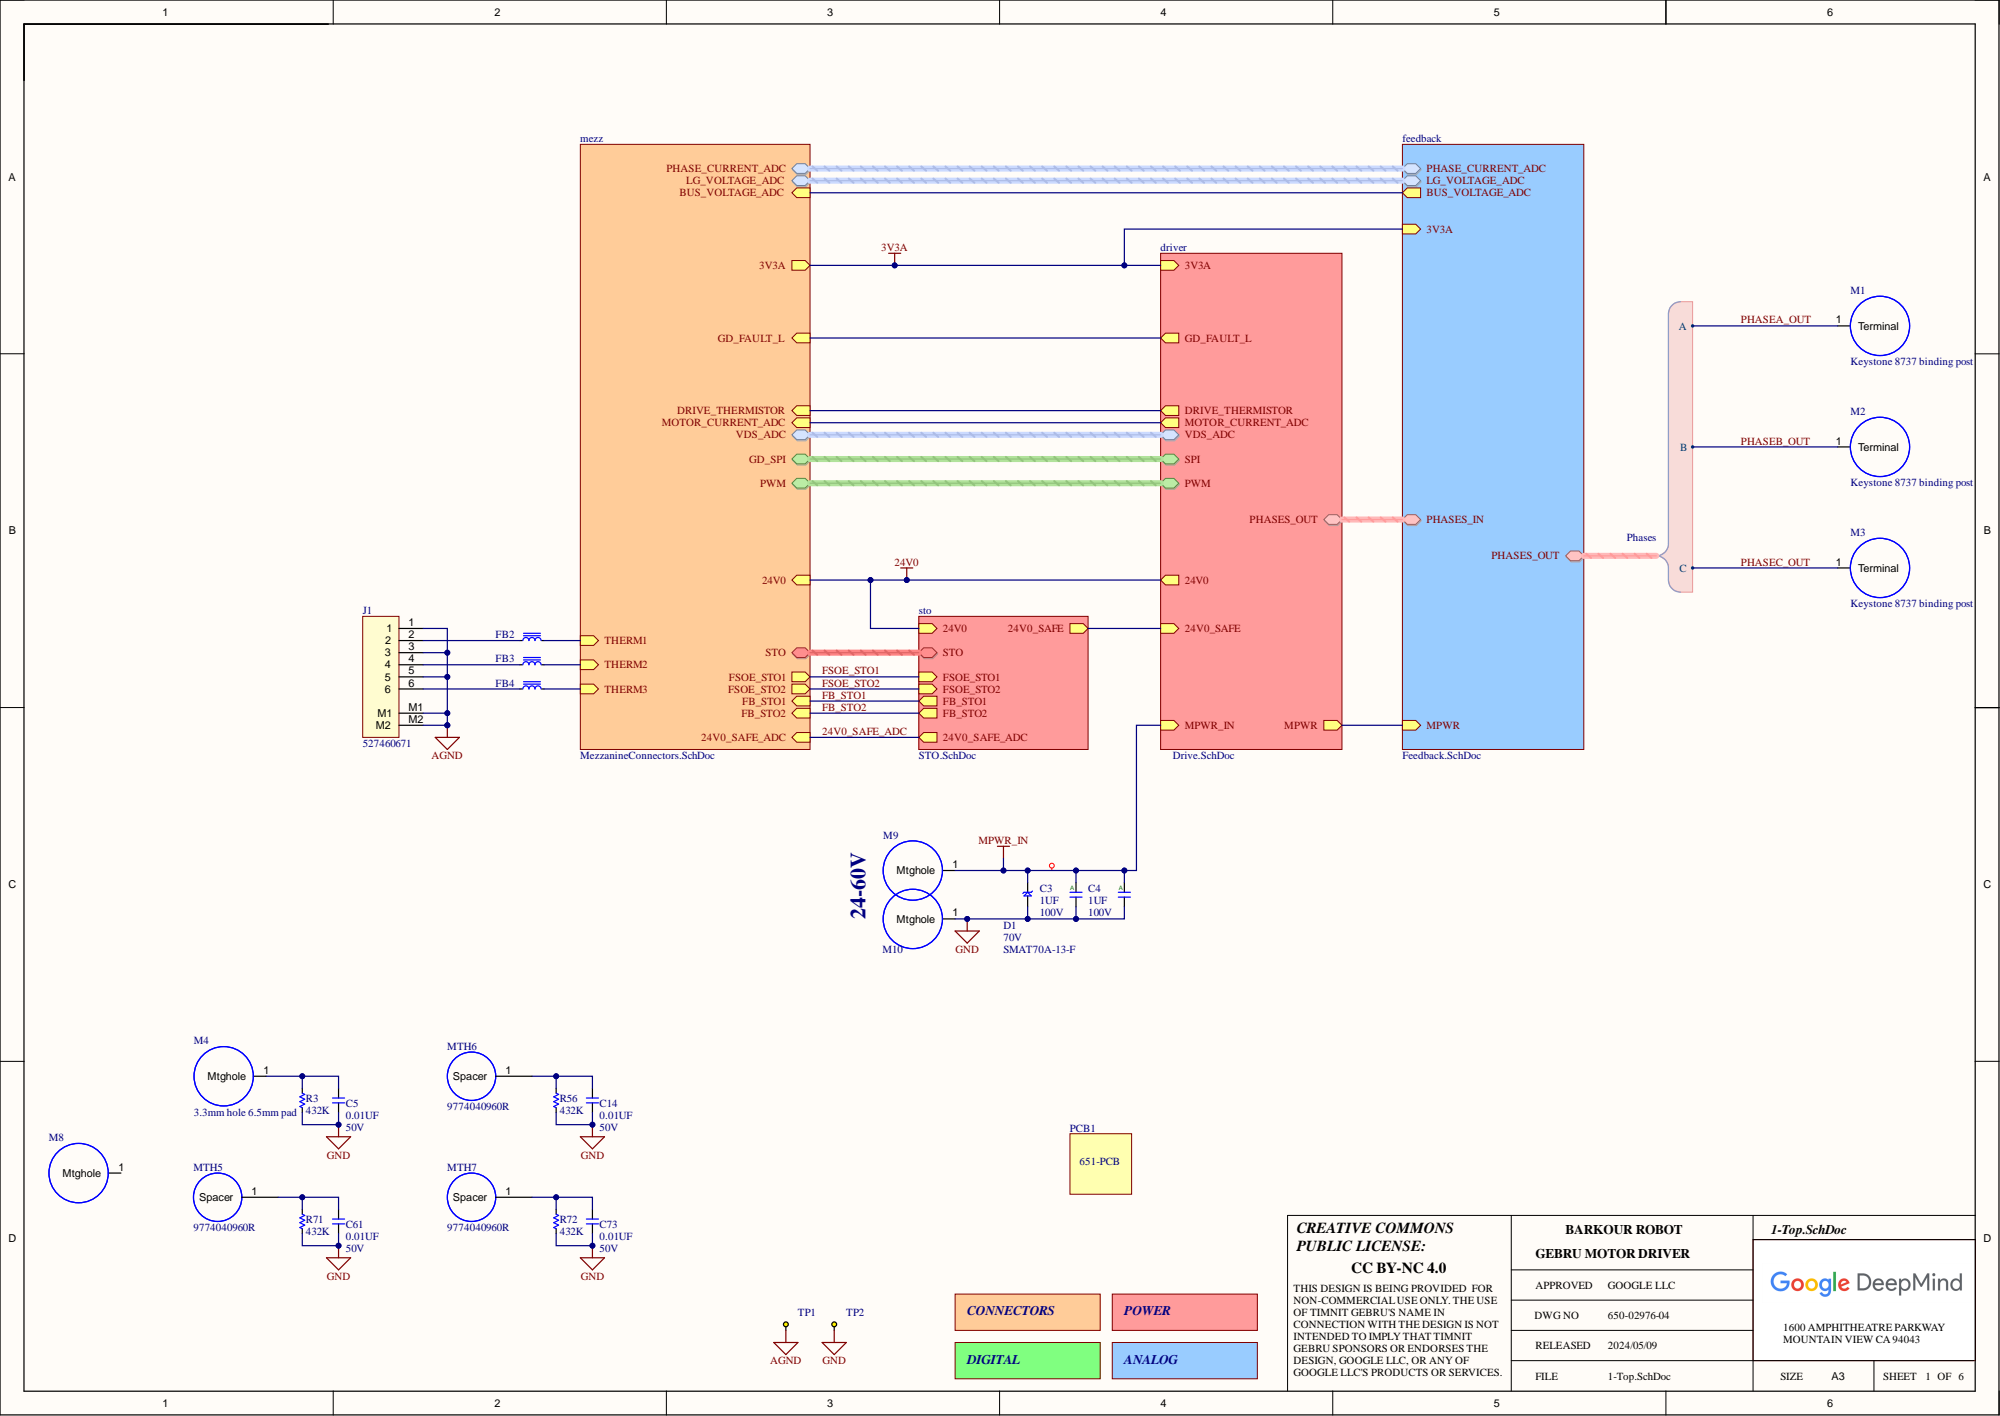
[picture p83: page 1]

THIS DESIGN IS BEING PROVIDED FOR
NON-COMMERCIALUSE ONLY. THE USE
OF TIMNIT GEBRU'S NAME IN
CONNECTION WITH THE DESIGN IS NOT
INTENDED TO IMPLY THAT TIMNIT
GEBRU SPONSORS OR ENDORSES THE
DESIGN, GOOGLE LLC, OR ANY OF
GOOGLE LLC'S PRODUCTS OR SERVICES.

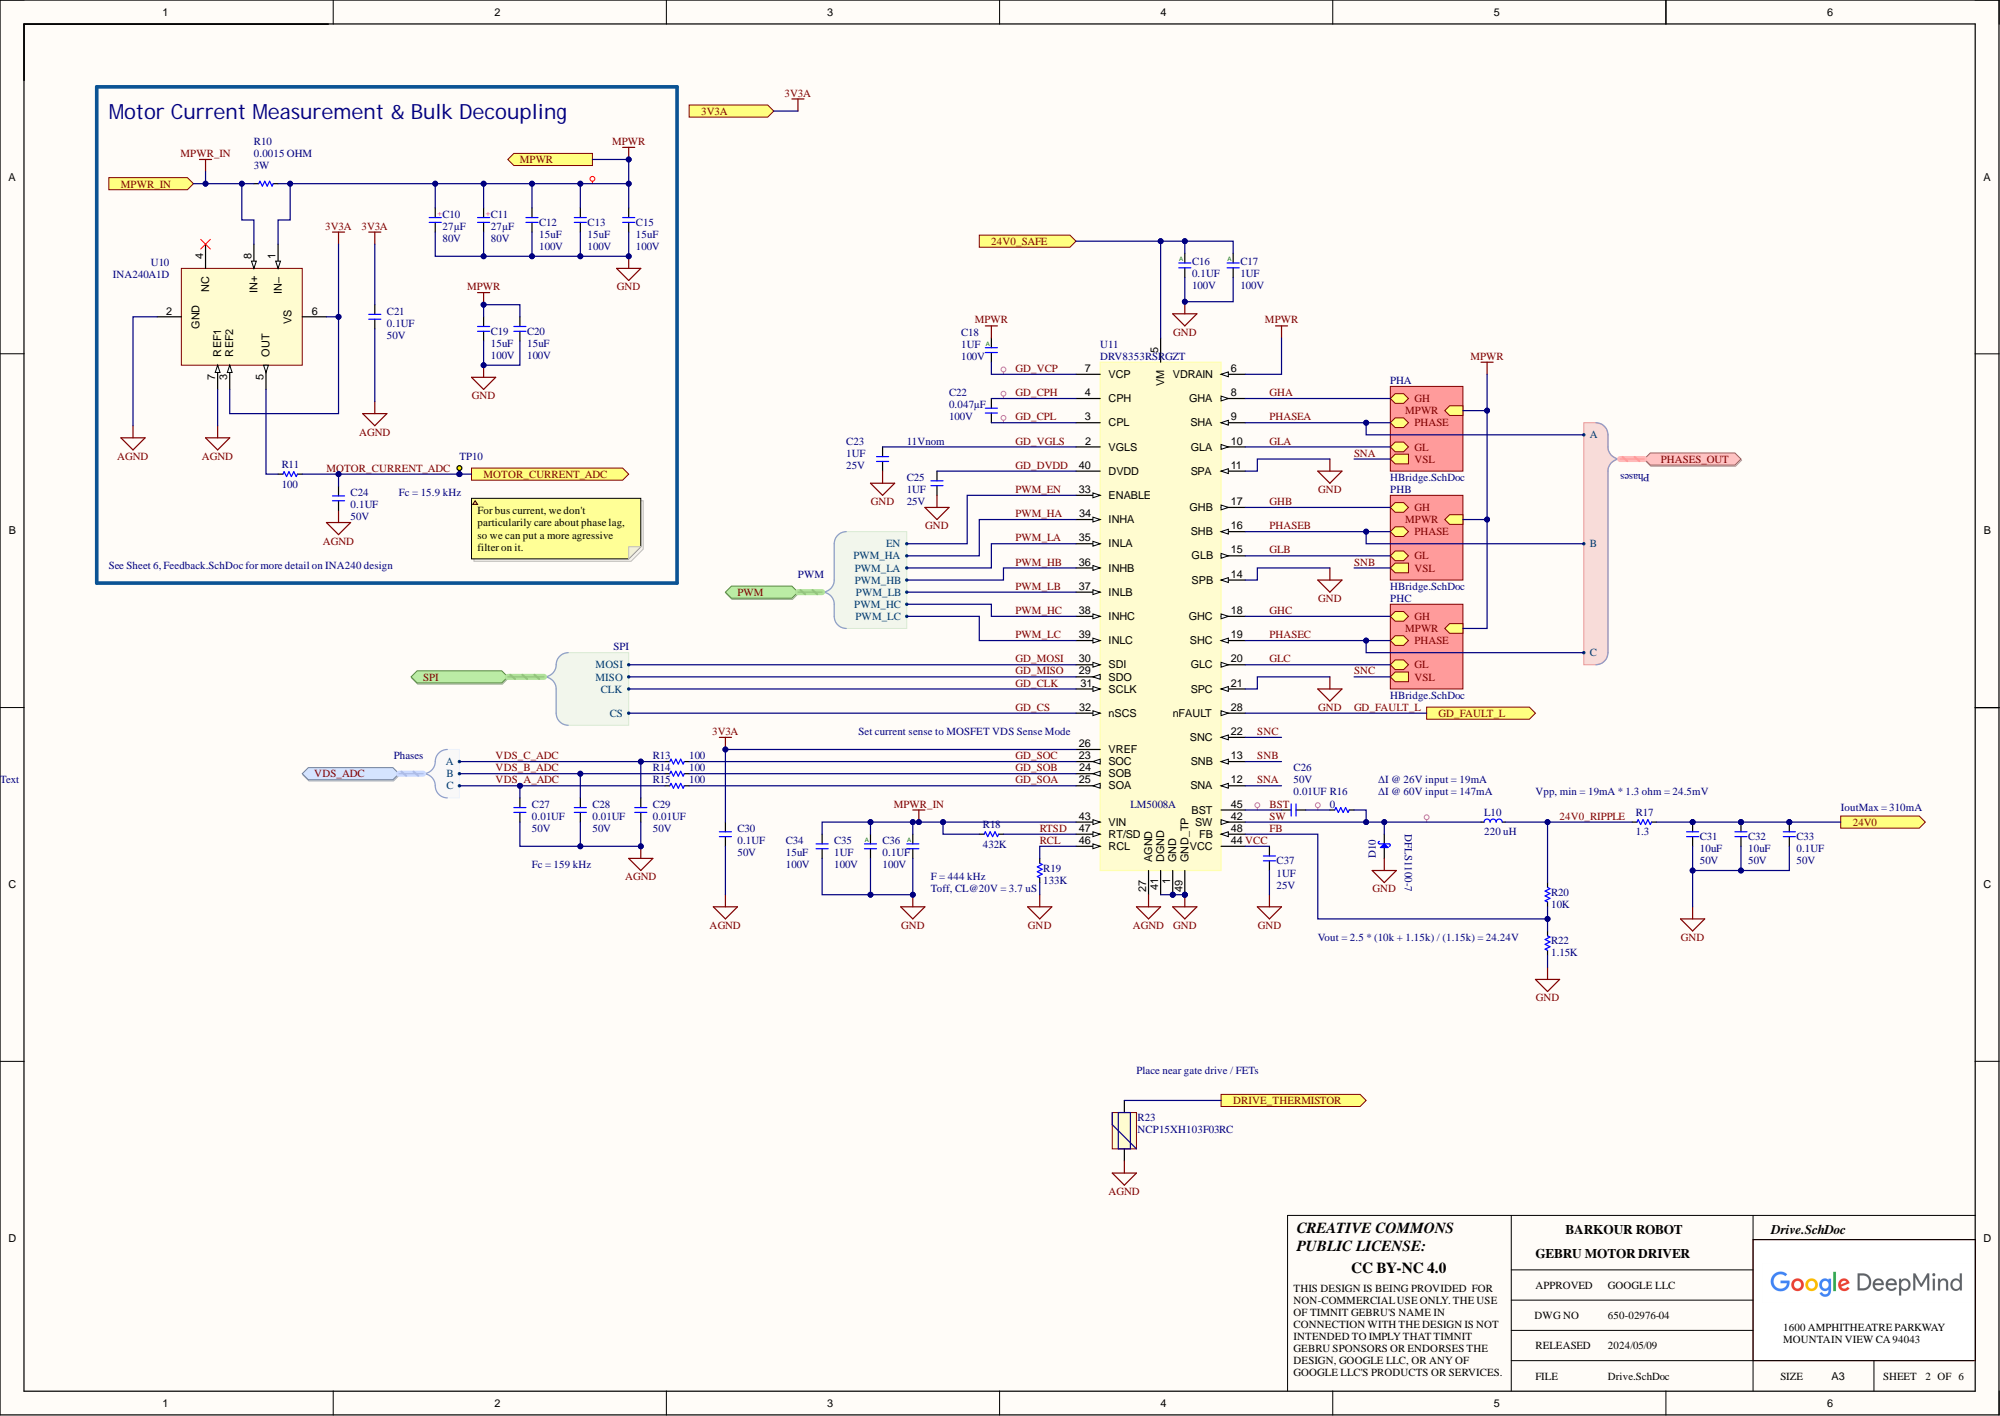
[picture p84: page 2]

Motor Current Measurement & Bulk Decoupling

For bus current, we don't
particularily care about phase lag,
so we can put a more agressive
filter on it.

PWM_HB | SNB

GLB

See Sheet 6, Feedback.SchDoc for more detail on INA240 design

INHC 38

PWM_LC | INLC 39 | PHASEC

Set current sense to MOSFET VDS Sense Mode

Place near gate drive / FETs

THIS DESIGN IS BEING PROVIDED FOR

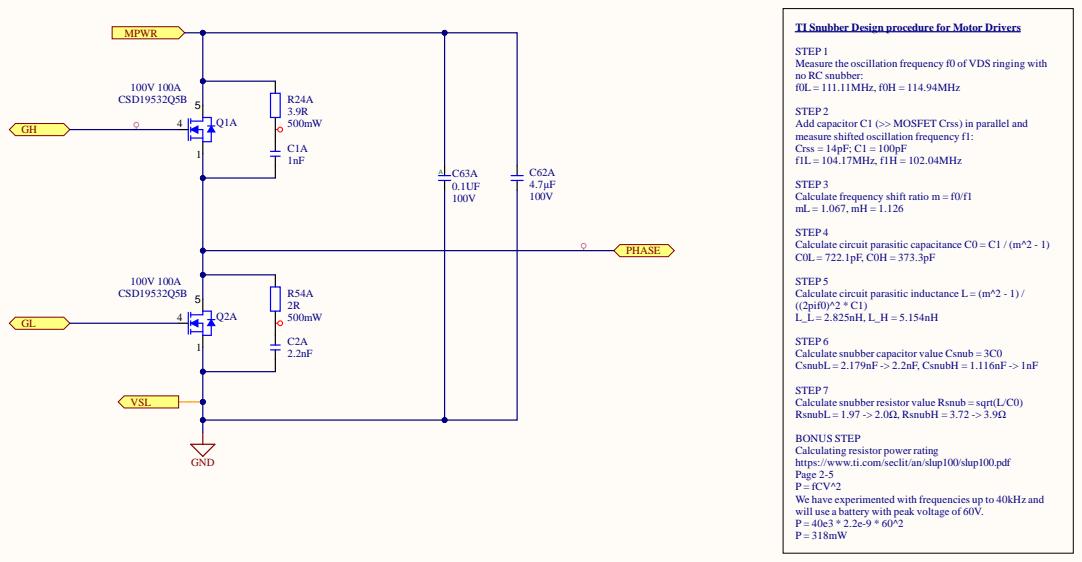
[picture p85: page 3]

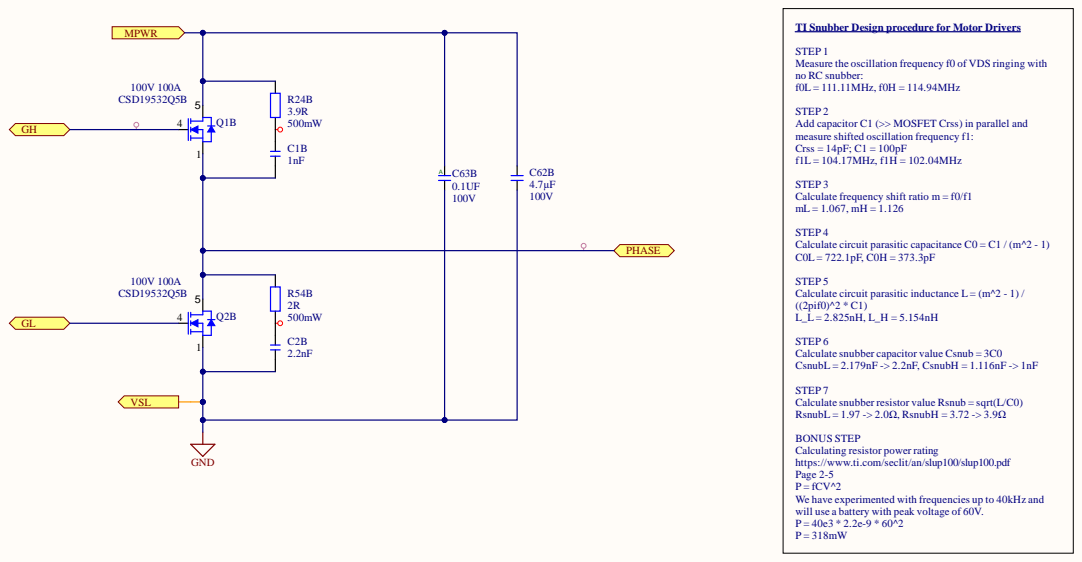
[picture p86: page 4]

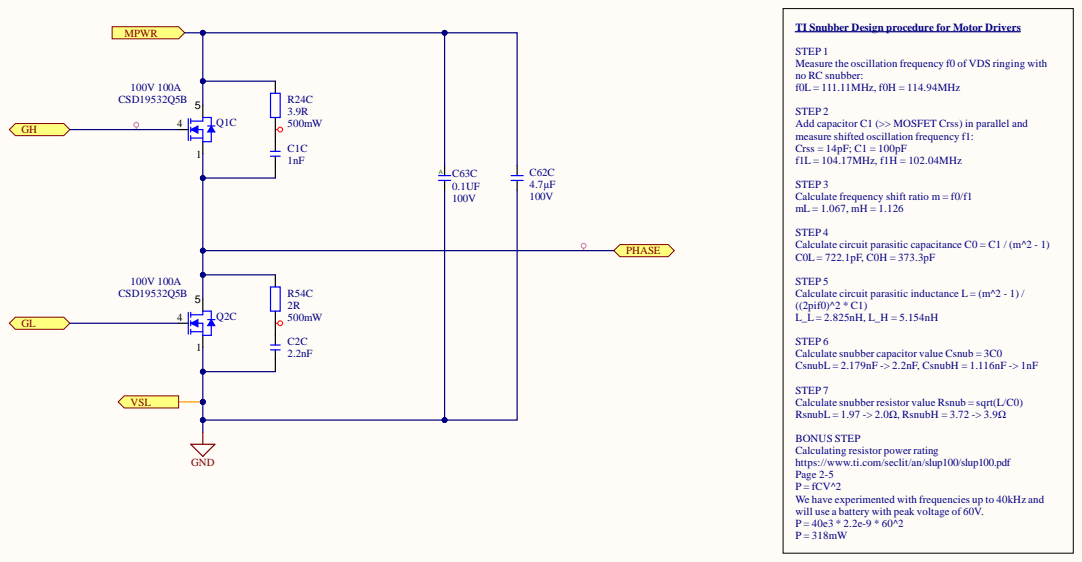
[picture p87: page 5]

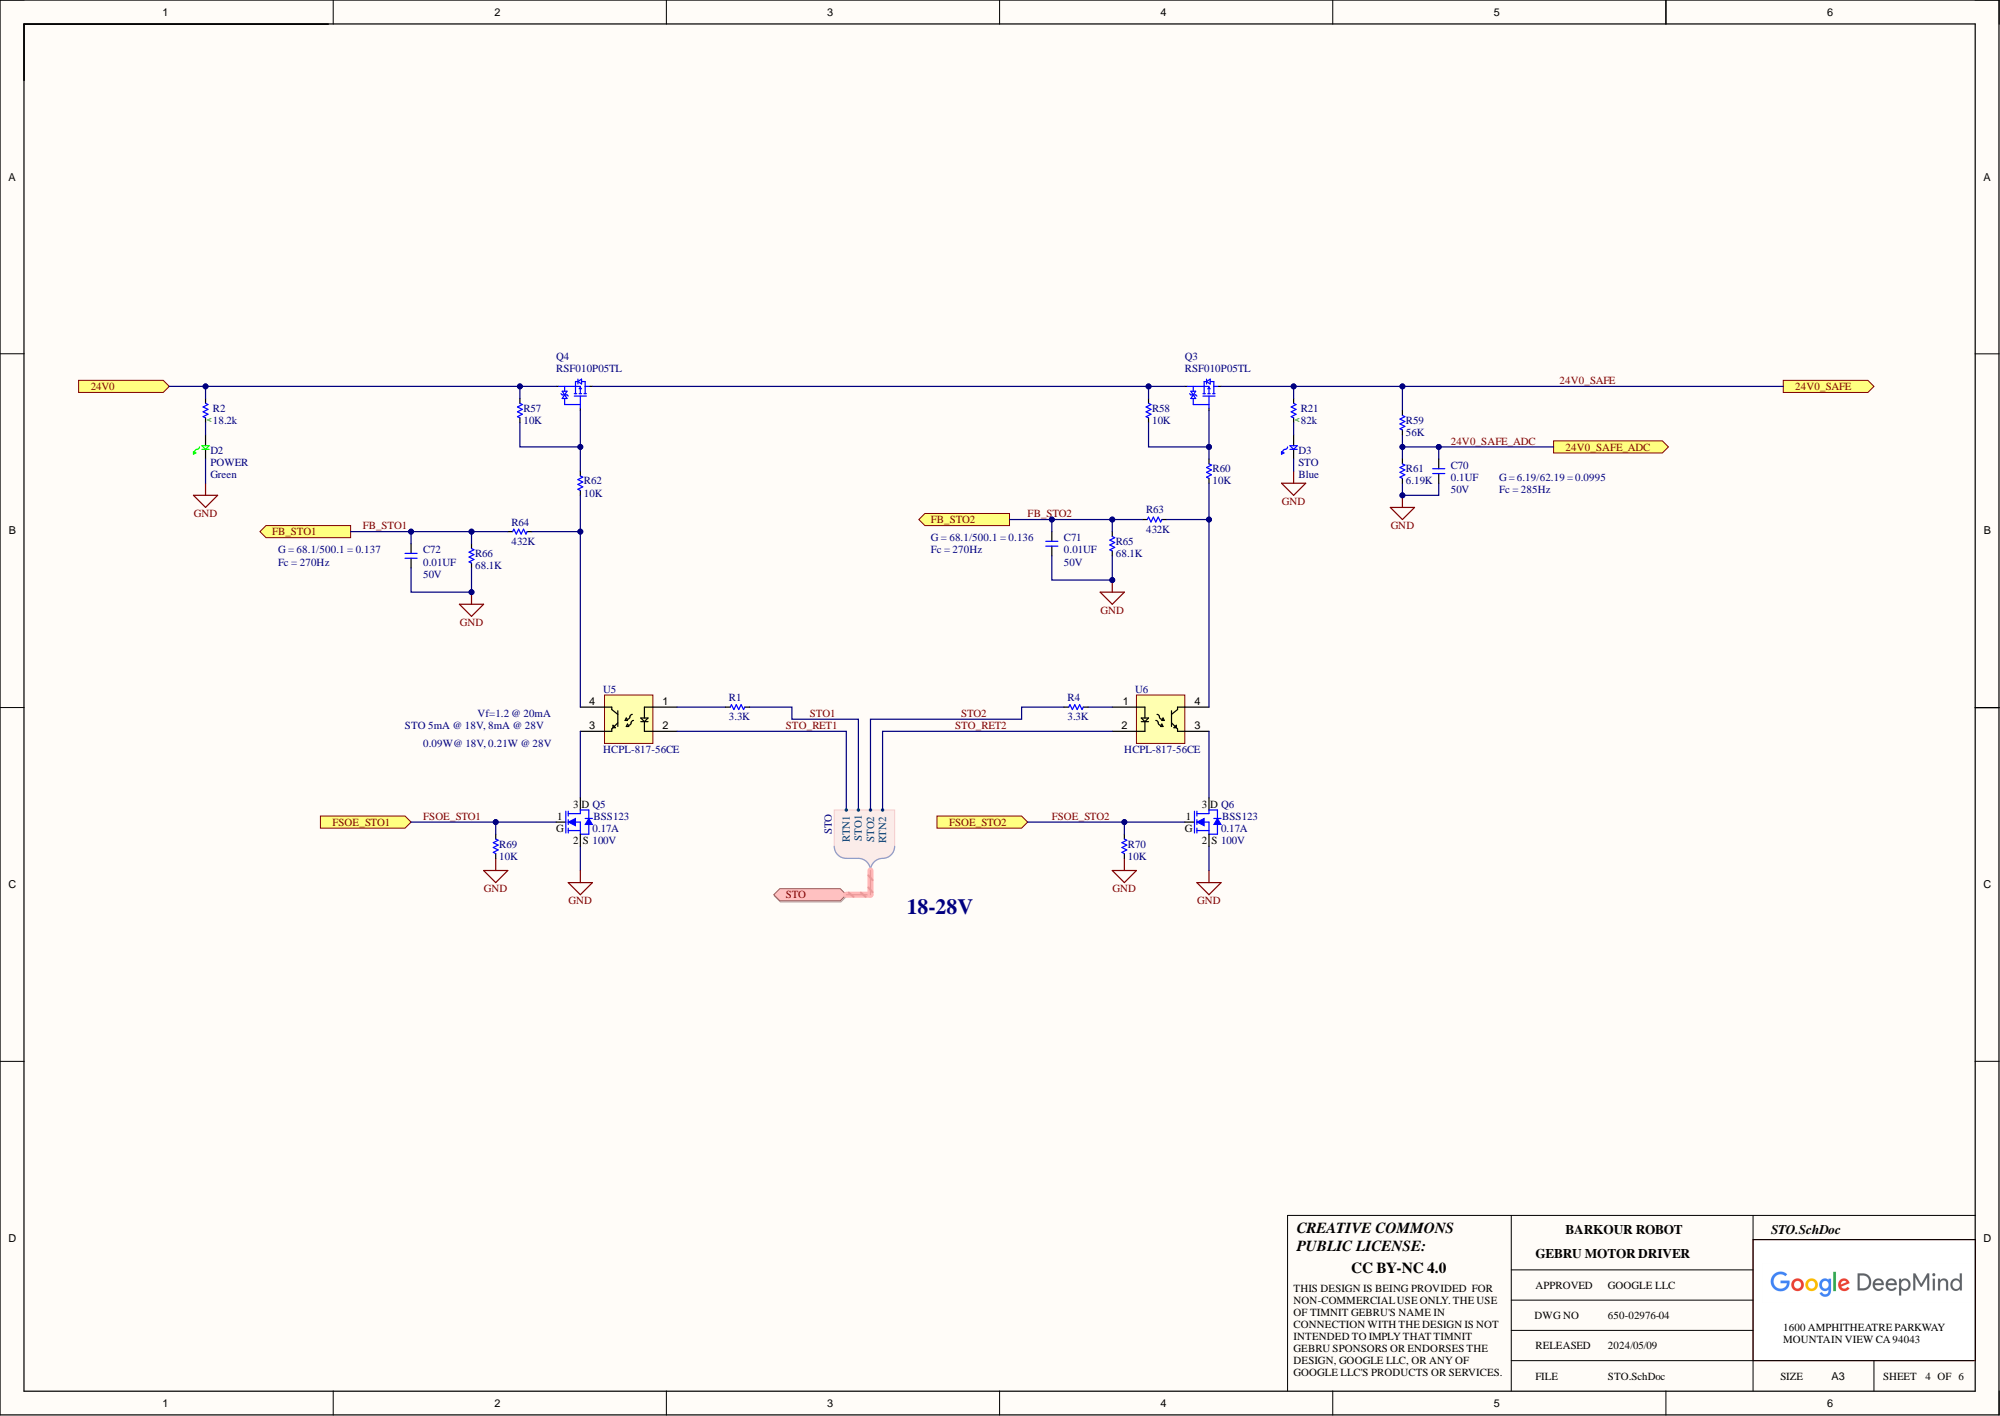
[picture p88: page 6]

THIS DESIGN IS BEING PROVIDED FOR

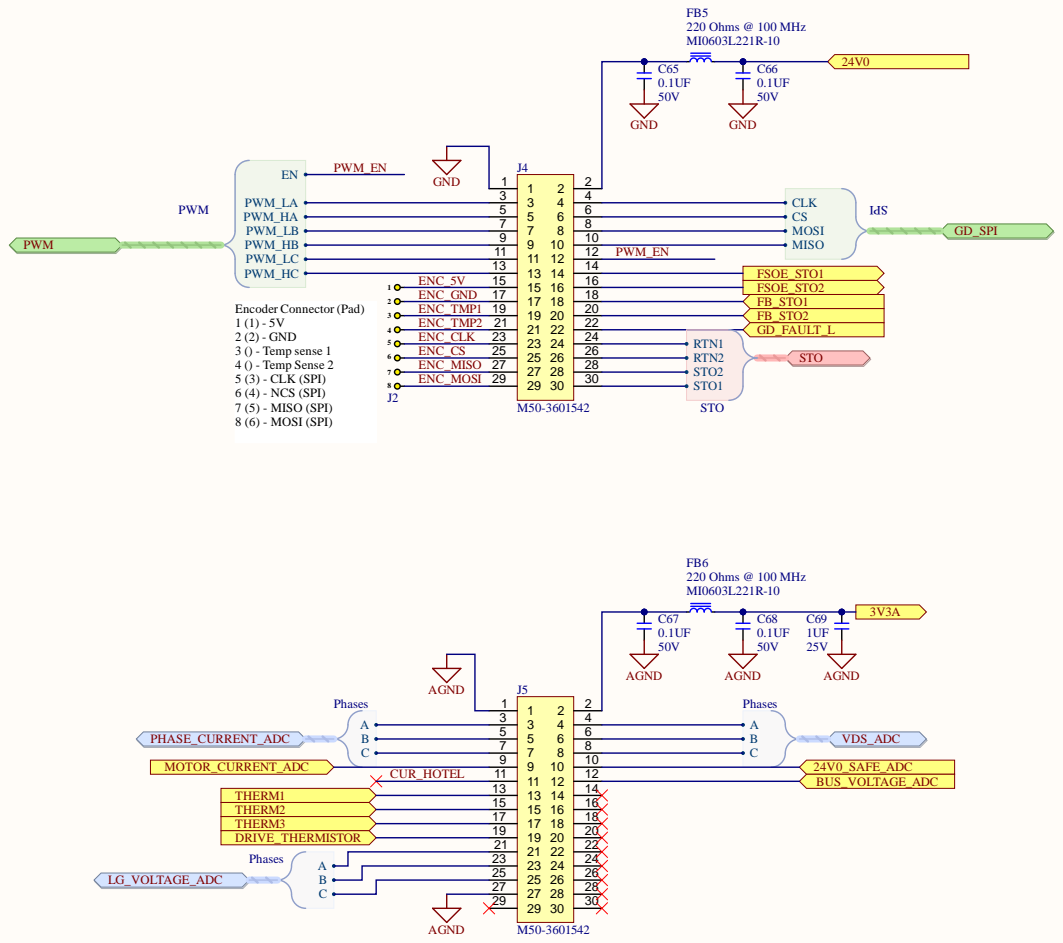
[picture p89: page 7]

THIS DESIGN IS BEING PROVIDED FOR


TO CONVERT OUTPUT VOLTAGE TO CURRENT: I_PHASE = (VOUT - 1.65) / 0.03

THIS DESIGN IS BEING PROVIDED FOR














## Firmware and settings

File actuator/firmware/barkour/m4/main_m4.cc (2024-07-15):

// Copyright 2024 DeepMind Technologies Limited
//
// Licensed under the Apache License, Version 2.0 (the "License");
// you may not use this file except in compliance with the License.
// You may obtain a copy of the License at
//
//    http://www.apache.org/licenses/LICENSE-2.0
//
// Unless required by applicable law or agreed to in writing, software
// distributed under the License is distributed on an "AS IS" BASIS,
// WITHOUT WARRANTIES OR CONDITIONS OF ANY KIND, either express or implied.
// See the License for the specific language governing permissions and
// limitations under the License.
// ==============================================================================

#include <stdbool.h>
#include <cstdint>
#include <cstdio>
#include <cmath>
#include <cstring>

#include "actuator/firmware/barkour/common/barkour_system.h"
#include "actuator/firmware/barkour/common/async_uart_logger.h"
#include "actuator/firmware/barkour/common/board_config.h"
#include "actuator/firmware/barkour/common/code_version.h"
#include "actuator/firmware/barkour/common/cycle_counter.h"
#include "actuator/firmware/barkour/common/interfaces/rotary_encoder_interface.h"
#include "actuator/firmware/barkour/common/multiturn_encoder_wrapper.h"
#include "actuator/firmware/barkour/drivers/stm32h7_hal/aksim2_encoder.h"
#include "actuator/firmware/barkour/drivers/stm32h7_hal/ma732_encoder.h"
#include "actuator/firmware/barkour/m4/board_setup_m4.h"
#include "actuator/firmware/barkour/m4/controller_thread.h"
#include "actuator/firmware/barkour/m4/ecat/utypes.h"
#include "actuator/firmware/barkour/m4/ecat_device.h"
#include "actuator/firmware/barkour/m4/gpio.h"
#include "pw_assert/check.h"
#include "pw_function/function.h"
#include "pw_log/log.h"
#include "pw_result/result.h"
#include "pw_system/init.h"
#include "pw_thread/detached_thread.h"
#include "FreeRTOS.h" // NOLINT
#include "task.h" // NOLINT

#if defined UNIT_TESTS_ENABLED || defined FUNCTIONAL_TESTS_ENABLED
#include "actuator/firmware/barkour/common/test_runner.h"
#endif

#define HSEM_ID_0 (0U)

// Number of bytes allocated to the stack of each RTOS.
constexpr uint16_t kLoggingTaskStackSizeBytes = 1024;
constexpr uint16_t kMainTaskStackSizeBytes = 2048;

// If something goes wrong in initialization, then enter prvErrorHandler.
// Presently, the handler does nothing, and will spin forever.
static void prvErrorHandler(void);

// Low-priority task for handling asynchronous logging.
static void prvLoggingTask(void* pvParameters);

// Primary FreeRTOS task function for the M4 core.
static void prvMainTask(void* pvParameters);

// FreeRTOS tasks
std::array<StackType_t, configMINIMAL_STACK_SIZE> freertos_idle_stack;
StaticTask_t freertos_idle_tcb;

StaticTask_t main_tcb;
std::array<StackType_t, kMainTaskStackSizeBytes> main_task_stack;

StaticTask_t logging_tcb;
std::array<StackType_t, kLoggingTaskStackSizeBytes> logging_task_stack;

UART_HandleTypeDef UartHandle;

int main(void) {
  __HAL_RCC_HSEM_CLK_ENABLE();
  HAL_HSEM_ActivateNotification(__HAL_HSEM_SEMID_TO_MASK(HSEM_ID_0));
  HAL_PWREx_ClearPendingEvent();
  HAL_PWREx_EnterSTOPMode(PWR_MAINREGULATOR_ON, PWR_STOPENTRY_WFE,
                          PWR_D2_DOMAIN);
  __HAL_HSEM_CLEAR_FLAG(__HAL_HSEM_SEMID_TO_MASK(HSEM_ID_0));

  if (HAL_Init() != HAL_OK) {
    prvErrorHandler();
  }

  // Enable synchronous logging prior to starting the scheduler and
  // M4LoggingTask.
  barkour::AsyncUartLogger::Get().DisableAsynchronousLogging();
  PW_LOG_INFO("Booting");
  PW_LOG_INFO("Setting up GPIO");
  barkour::SetupGPIO();

  FLASH_OBProgramInitTypeDef init_config;
  HAL_FLASHEx_OBGetConfig(&init_config);
  PW_LOG_DEBUG("M4 boot address 0 %#lx", init_config.CM4BootAddr0);
  PW_LOG_DEBUG("M7 boot address 0 %#lx", init_config.BootAddr0);

  if (HAL_FLASH_OB_Unlock() != HAL_OK) {
    PW_LOG_ERROR("HAL_FLASH_OB_Unlock failed. Could not unlock option bytes.");
  }
  // Retrieves the dual boot configuration status.
  FLASH_OBProgramInitTypeDef OBInit;

  OBInit.Banks = FLASH_BANK_1;
  HAL_FLASHEx_OBGetConfig(&OBInit);

  if ((OBInit.USERConfig & OB_SWAP_BANK_ENABLE) == OB_SWAP_BANK_DISABLE) {
    PW_LOG_INFO("Memory banks not swapped.");
  } else {
    PW_LOG_INFO("Memory banks swapped.");
  }
  if (HAL_FLASH_OB_Lock() != HAL_OK) {
    PW_LOG_ERROR("HAL_FLASH_OB_Lock failed. Could not lock option bytes.");
  }

  // Important: Set the address of the interrupt vector table.
  // This is located at the start of the ROM.
  // By default this value is 0, meaning the M4 will point its
  // interrupts to the M7's, which results in a less than optimal
  // experience.
  uint32_t* vtor = reinterpret_cast<uint32_t*>(0xE000ED08);
  *vtor = init_config.CM4BootAddr0;

  barkour::CycleCounter::Get().Enable();

  xTaskCreateStatic(prvLoggingTask, "M4LoggingTask", logging_task_stack.size(),
                    NULL, tskIDLE_PRIORITY + 1, logging_task_stack.data(),
                    &logging_tcb);
  xTaskCreateStatic(prvMainTask, "MainTask", main_task_stack.size(), NULL,
                    tskIDLE_PRIORITY + 2, main_task_stack.data(), &main_tcb);

  barkour::GPIO::Get().EnableInterrupts();

  // Start Pigweed logging, RPC and work queue threads.
  pw::system::Init();

  // This modules provides target-agnostic interfaces to hardware-backed
  // components used by the Barkour Motor Controller.

  // Initializes target-agnostic interfaces to hardware-backed components used
  // by the Barkour Motor Controller.
  PW_CHECK_OK(barkour::System::Get().Initialize());

  // Starts the FreeRTOS scheduler.
  vTaskStartScheduler();
}

// This will run once after pw::system::Init() completes. This callback must
// return or it will block the work queue.
//
// This is the first thing run in a threaded context (specifically on the work
// queue thread).
namespace pw::system {
void UserAppInit() {}
}  // namespace pw::system

static void prvErrorHandler(void) {
  while (1) {
  }
}

static void prvLoggingTask(void* pvParameters) {
  barkour::AsyncUartLogger::Get().EnableAsynchronousLogging();
  while (1) {
    barkour::AsyncUartLogger::Get().Update();
    vTaskDelay(20);
  }
}
#if defined UNIT_TESTS_ENABLED || defined FUNCTIONAL_TESTS_ENABLED
// Sleep for a short amount of time after each test, to avoid overloading the
// logger.
void PostTestSleep(void) { vTaskDelay(pdMS_TO_TICKS(100)); }
#endif
static void prvMainTask(void* pvParameters) {
  PW_LOG_INFO("Firmware built with code version: %s", barkour::kCodeVersion);

#if defined UNIT_TESTS_ENABLED || defined FUNCTIONAL_TESTS_ENABLED
  barkour::run_tests(pw::Function<void()>(PostTestSleep));
  PW_LOG_INFO("All unit tests done");

  for (uint8_t x = 5; x; x--) {
    vTaskDelay(pdMS_TO_TICKS(100));
    PW_LOG_INFO(" ");  // Flush the log.
  }
  barkour::BoardConfig::Get().DisableMotorPower();

  while (1) {
    vTaskDelay(pdMS_TO_TICKS(10));
  }

#endif

#if ENCODER_TYPE == ENCODER_MA732_ADA
  barkour::RotaryEncoder& encoder = barkour::Ma732Encoder::Get();
#elif ENCODER_TYPE == ENCODER_RLS_AKSIM2
  barkour::RotaryEncoder& encoder = barkour::AksIm2Encoder::Get();
#else
#error "Unknown encoder type."
#endif

  barkour::MultiturnEncoderWrapper encoder_wrapper(encoder);

  pw::sync::ThreadNotification controller_notification;
  pw::Result<barkour::TimerNotifierInterface*> maybe_timer_notifier =
      barkour::System::Get().GetControllerTimerNotifier();
  PW_CHECK_OK(maybe_timer_notifier.status());
  PW_CHECK_OK(maybe_timer_notifier.value()->RegisterThreadNotification(
      controller_notification));
  PW_CHECK_OK(maybe_timer_notifier.value()->Start());

  // Start controller thread.
  barkour::ControllerThread controller_thread(
      encoder_wrapper, controller_notification,
      1.0f / barkour::kControllerTimerNotifierUpdateFrequencyHz);
  pw::thread::DetachedThread(
      barkour::System::Get().GetControllerThreadOptions(), controller_thread);

  barkour::EthercatDevice& ecat_device = barkour::EthercatDevice::Get();
  ecat_device.Run();
}

extern "C" {
// Provides the stack overflow hook function used by FreeRTOS.
//
// This functional will be called if configCHECK_FOR_STACK_OVERFLOW is defined
// to be 1 or 2, and a stack overflow is detected.
void vApplicationStackOverflowHook([[maybe_unused]] xTaskHandle xTask,
                                   char* pcTaskName) {
  // Because pcTaskName may be an improperly formed string due to memory
  // corruption, strncat is used to safely limit the amount of data that will be
  // printed to the screen in the crash report.
  static char safe_task_name[configMAX_TASK_NAME_LEN + 1] = {'\0'};
  strncat(safe_task_name, (const char*)pcTaskName, sizeof(safe_task_name) - 1);
  PW_CRASH("Stack overflow detected for task %s", safe_task_name);
}
// Provides pointers to FreeRTOS for the Idle task.
//
// This function is called when FreeRTOS is configured to support static memory
// allocation (configSUPPORT_STATIC_ALLOCATION).
void vApplicationGetIdleTaskMemory(StaticTask_t** ppxIdleTaskTCBBuffer,
                                   StackType_t** ppxIdleTaskStackBuffer,
                                   uint32_t* pulIdleTaskStackSize) {
  *ppxIdleTaskTCBBuffer = &freertos_idle_tcb;
  *ppxIdleTaskStackBuffer = freertos_idle_stack.data();
  *pulIdleTaskStackSize = freertos_idle_stack.size();
}
#if defined(__GNUC__)
// Note: Logging is asynchronous until the log buffer fills up,
// at which point we will switch permanently to synchronous logging.
int _write(int fd, char* ptr, int len) {
  pw::Status status;
  status = barkour::AsyncUartLogger::Get().Log({ptr, (size_t)len});
  if (status.IsResourceExhausted()) {
    // Resource is exhausted, dump the current buffer and switch to blocking
    // logging.
    barkour::AsyncUartLogger::Get().DisableAsynchronousLogging();
    PW_LOG_WARN("Logging ring buffer overflow. Asynchronous logging disabled.");
  }
  return len;
}
#endif
// Memory map of the flash data for reading.
__attribute__((section(".ap_m4_data.flash_data"))) char flash_data[128000];
}  // extern C.

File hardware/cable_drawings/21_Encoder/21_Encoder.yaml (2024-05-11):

options:
    mini_bom_mode: false

connectors:
    X1:
        # 1.25mm wire to board 8 way
        type: 10114826-00008LF
        pinlabels: [5V, GND, T+, T-, CLK, CS, MISO, MOSI]
        image:
            src: ../WireViz_Source/10114826-00008LF.png
            caption: 1.25mm Wire to Board Housing, 8 Positions
            height: 100
        notes: |
            1. Premade connector with flying leads available from RSI under P/N ACC049.
            2. To create from scratch use this connector P/N and crimps
        additional_components:
            -
                type: Crimp
                subtype: MiniTek 1.25 female, gold, 28-32 AWG
                manufacturer: Amphenol ICC
                mpn: 10114827-004-LF
                qty_multiplier: populated

    X2:
        # Soldered connection
        type: Gebru V5 - J2, soldered connection
        pinlabels: [5V, GND, T+, T-, CLK, CS, MISO, MOSI]
        notes: |
            Strip wires 2mm from ends.

cables:
    W1:
        # 8 wire preassembly
        wirecount: 8
        colors: [BN, WH, PK, GY, RD, BU, GN, YE]
        gauge: 30 AWG # also accepts AWG as unit
        shield: false
        length: 50 mm
        manufacturer: RSI
        mpn: ACC049
        notes: |
            1. Comes with 10114826-00008LF connector attached.
            2. Add label "AP Encoder".

connections:
    -
        - X1: [1,2,3,4,5,6,7,8]
        - W1: [1,2,3,4,5,6,7,8]
        - X2: [1,2,3,4,5,6,7,8]

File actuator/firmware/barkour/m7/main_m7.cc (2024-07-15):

// Copyright 2024 DeepMind Technologies Limited
//
// Licensed under the Apache License, Version 2.0 (the "License");
// you may not use this file except in compliance with the License.
// You may obtain a copy of the License at
//
//    http://www.apache.org/licenses/LICENSE-2.0
//
// Unless required by applicable law or agreed to in writing, software
// distributed under the License is distributed on an "AS IS" BASIS,
// WITHOUT WARRANTIES OR CONDITIONS OF ANY KIND, either express or implied.
// See the License for the specific language governing permissions and
// limitations under the License.
// ==============================================================================

#include <array>
#include <cstdint>
#include <cstring>
#include <cstdio>

#include "actuator/firmware/barkour/common/shared_memory.h"
#include "actuator/firmware/barkour/m7/board_setup_m7.h"
#include "FreeRTOS.h" // NOLINT
#include "task.h" // NOLINT
#include "stm32h7xx_hal.h" // NOLINT
#include "pw_assert/check.h"
#include "pw_system/init.h"

#define HSEM_ID_0 (0U)
constexpr int kMainTaskStackSizeBytes = 1024;

// If something goes wrong during initialisation, then enter prvErrorHandler.
// Presently, the handler does nothing, and will spin forever.
static void prvErrorHandler(void);

// Primary FreeRTOS task function for the M7 core.
// Presently blinks LED1 to indicate that the FreeRTOS kernel is operating.
static void prvM7MainTask(void* pvParameters);

// FreeRTOS tasks
std::array<StackType_t, configMINIMAL_STACK_SIZE> freertos_idle_stack;
StaticTask_t freertos_idle_tcb;

StaticTask_t main_tcb;
std::array<StackType_t, kMainTaskStackSizeBytes> main_task_stack;

int main(void) {
  barkour::MPU_Config();
  barkour::CPU_CACHE_Enable();

  // Copy the Unique ID from system memory (only accessible by the M7 core) to
  // shared memory.

  // Fixed address, from the STM32h745/755 reference manual.
  uint32_t* kStm32UniqueIdBaseAddress =
      reinterpret_cast<uint32_t*>(0x1ff1'e800);

  std::memcpy(reinterpret_cast<uint32_t*>(barkour::kUidWord0Address),
              kStm32UniqueIdBaseAddress, sizeof(uint32_t));
  std::memcpy(reinterpret_cast<uint32_t*>(barkour::kUidWord1Address),
              kStm32UniqueIdBaseAddress + 1, sizeof(uint32_t));
  std::memcpy(reinterpret_cast<uint32_t*>(barkour::kUidWord2Address),
              kStm32UniqueIdBaseAddress + 2, sizeof(uint32_t));

  // Wait for M4 to boot and enter STOP mode.
  while (__HAL_RCC_GET_FLAG(RCC_FLAG_D2CKRDY) != RESET) {
  }

  if (HAL_Init() != HAL_OK) {
    prvErrorHandler();
  }

  // If the boot addresses for the M4 and M7 do not match the
  // start of the program memory (see linker files), we will
  // update them and reboot the device.
  // In particular, the M4 boots up from 0x08100000 by default,
  // which doesn't match the FoE firmware update setup.

  FLASH_OBProgramInitTypeDef init_config;
  HAL_FLASHEx_OBGetConfig(&init_config);
  uint32_t m4_boot_add_0 = init_config.CM4BootAddr0;
  uint32_t m7_boot_add_0 = init_config.BootAddr0;

  const uint32_t m4_boot_add_0_default = 0x08080000;
  const uint32_t m7_boot_add_0_default = 0x08000000;

  if (m4_boot_add_0 == m4_boot_add_0_default &&
      m7_boot_add_0 == m7_boot_add_0_default) {
    // Valid.
  } else {
    // Invalid. Write boot addresses.
    HAL_FLASH_Unlock();
    HAL_FLASH_OB_Unlock();
    FLASH_OBProgramInitTypeDef boot_options_m4;
    boot_options_m4.OptionType = OPTIONBYTE_CM4_BOOTADD;
    boot_options_m4.CM4BootConfig = OB_BOOT_ADD0;
    boot_options_m4.CM4BootAddr0 = m4_boot_add_0_default;

    FLASH_OBProgramInitTypeDef boot_options_m7 = boot_options_m4;
    boot_options_m7.OptionType |= OPTIONBYTE_CM7_BOOTADD;
    boot_options_m7.BootConfig = OB_BOOT_ADD0;
    boot_options_m7.BootAddr0 = m7_boot_add_0_default;
    HAL_FLASHEx_OBProgram(&boot_options_m7);
    HAL_FLASH_OB_Launch();
    HAL_FLASH_OB_Lock();
    HAL_FLASH_Lock();

    // Reboot if a write occurred, to make sure the M4 can boot correctly.
    NVIC_SystemReset();
  }

  barkour::SystemClock_Config();

  // Upon releasing the HSEM, CM4 will wake up from STOP mode.
  __HAL_RCC_HSEM_CLK_ENABLE();
  HAL_HSEM_FastTake(HSEM_ID_0);
  HAL_HSEM_Release(HSEM_ID_0, 0);

  xTaskCreateStatic(prvM7MainTask, "MainTask", main_task_stack.size(), NULL,
                    tskIDLE_PRIORITY + 1, main_task_stack.data(), &main_tcb);

  // Start Pigweed logging, RPC and work queue threads.
  pw::system::Init();

  // Start the FreeRTOS scheduler.
  vTaskStartScheduler();

  while (1) {
  }
}

// This will run once after pw::system::Init() completes. This callback must
// return or it will block the work queue.
//
// This is the first thing run in a threaded context (specifically on the work
// queue thread).
namespace pw::system {
void UserAppInit() {}
}  // namespace pw::system

static void prvM7MainTask(void* pvParameters) {
  TickType_t xNextWakeTime;
  const TickType_t xCycleFrequency = pdMS_TO_TICKS(500UL);
  xNextWakeTime = xTaskGetTickCount();

  for (;;) {
    vTaskDelayUntil(&xNextWakeTime, xCycleFrequency);
  }
}

static void prvErrorHandler(void) {
  while (1) {
  }
}

extern "C" {

// Provides the stack overflow hook function used by FreeRTOS.
//
// This functional will be called if configCHECK_FOR_STACK_OVERFLOW is defined
// to be 1 or 2, and a stack overflow is detected.
void vApplicationStackOverflowHook([[maybe_unused]] xTaskHandle xTask,
                                   char* pcTaskName) {
  static char safe_task_name[configMAX_TASK_NAME_LEN + 1] = {'\0'};
  strncat(safe_task_name, (const char*)pcTaskName, sizeof(safe_task_name) - 1);
  PW_CRASH("Stack overflow detected for task %s", safe_task_name);
}

// Provides pointers to FreeRTOS for the Idle task.
//
// This function is called when FreeRTOS is configured to support static memory
// allocation (configSUPPORT_STATIC_ALLOCATION).
void vApplicationGetIdleTaskMemory(StaticTask_t** ppxIdleTaskTCBBuffer,
                                   StackType_t** ppxIdleTaskStackBuffer,
                                   uint32_t* pulIdleTaskStackSize) {
  *ppxIdleTaskTCBBuffer = &freertos_idle_tcb;
  *ppxIdleTaskStackBuffer = freertos_idle_stack.data();
  *pulIdleTaskStackSize = freertos_idle_stack.size();
}

}  // extern C.

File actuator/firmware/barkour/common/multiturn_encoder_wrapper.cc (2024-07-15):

// Copyright 2024 DeepMind Technologies Limited
//
// Licensed under the Apache License, Version 2.0 (the "License");
// you may not use this file except in compliance with the License.
// You may obtain a copy of the License at
//
//    http://www.apache.org/licenses/LICENSE-2.0
//
// Unless required by applicable law or agreed to in writing, software
// distributed under the License is distributed on an "AS IS" BASIS,
// WITHOUT WARRANTIES OR CONDITIONS OF ANY KIND, either express or implied.
// See the License for the specific language governing permissions and
// limitations under the License.
// ==============================================================================

#include "actuator/firmware/barkour/common/multiturn_encoder_wrapper.h"

#include <cstdint>
#include <cstdlib>
#include <limits>

#include "actuator/firmware/barkour/common/interfaces/rotary_encoder_interface.h"
#include "pw_log/log.h"
#include "pw_result/result.h"

namespace barkour {

MultiturnEncoderWrapper::MultiturnEncoderWrapper(RotaryEncoder& base_encoder)
    : base_encoder_(base_encoder),
      base_encoder_counts_per_turn_(base_encoder_.GetCountsPerTurn()) {
  if (base_encoder_counts_per_turn_ >
      static_cast<uint32_t>(std::numeric_limits<int32_t>::max())) {
    PW_LOG_WARN(
        "MultiturnEncoderWrapper got a base encoder with counts per turn "
        "higher than INT32_MAX. This might result in incorrect calculations.");
  }
}

pw::Result<RotaryEncoderState> MultiturnEncoderWrapper::GetEncoderState() {
  return base_encoder_.GetEncoderState();
}

RotaryEncoderState& MultiturnEncoderWrapper::GetEncoderStateFromISR() {
  return base_encoder_.GetEncoderStateFromISR();
}

// Called from ISR.
pw::Result<RotaryEncoderState> MultiturnEncoderWrapper::Update() {
  pw::Result<RotaryEncoderState> result = base_encoder_.Update();
  if (!result.ok()) {
    return result;
  }

  // Get reference to actual base_encoder data structure so it can be updated.
  RotaryEncoderState& base_encoder_state = GetEncoderStateFromISR();

  if (!previous_encoder_counts_.has_value()) {
    previous_encoder_counts_ = base_encoder_state.raw_encoder_counts;
    base_encoder_state.multiturn_encoder_counts =
        previous_encoder_counts_.value();
  }

  int32_t previous_shaft_counts_normed =
      previous_encoder_counts_.value() % base_encoder_counts_per_turn_;

  int32_t displacement =
      base_encoder_state.raw_encoder_counts - previous_shaft_counts_normed;

  if (static_cast<uint32_t>(std::abs(displacement)) >
      base_encoder_counts_per_turn_ / 2) {
    if (displacement < 0) {
      // Positive-headed rollover occurred.
      displacement += base_encoder_counts_per_turn_;
    } else {
      // Negative-headed rollover occurred.
      displacement -= base_encoder_counts_per_turn_;
    }
  }
  int32_t new_shaft_counts = previous_encoder_counts_.value() + displacement;

  // if (!(std::abs(new_shaft_counts - previous_encoder_counts_.value()) <
  //      std::numeric_limits<int32_t>::max() / 2)) {
  // }

  previous_encoder_counts_ = new_shaft_counts;

  // Add multiturn information.
  base_encoder_state.multiturn_encoder_counts = new_shaft_counts;

  result = base_encoder_state;
  return result;
}

uint32_t MultiturnEncoderWrapper::GetCountsPerTurn() const {
  return base_encoder_counts_per_turn_;
}

}  // namespace barkour

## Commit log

2024-05-13 Update README.md
    Updated CAD links that were broken.
2024-05-13 Add missing Holberton PCBA design.
    [1-Holberton_Child_Top.SchDoc, 1-Holberton_TOP.SchDoc, Accelerometer.SchDoc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]
